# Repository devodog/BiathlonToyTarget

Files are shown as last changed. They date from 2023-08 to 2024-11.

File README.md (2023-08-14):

# Introduction

Watching the biathlon world cup events on tv and sensing the thrill and
excitement of the athletes skiing and especially the shooting
performance, an idea of making a similar toy shooting range target
arrangement for nerf gun, was born.

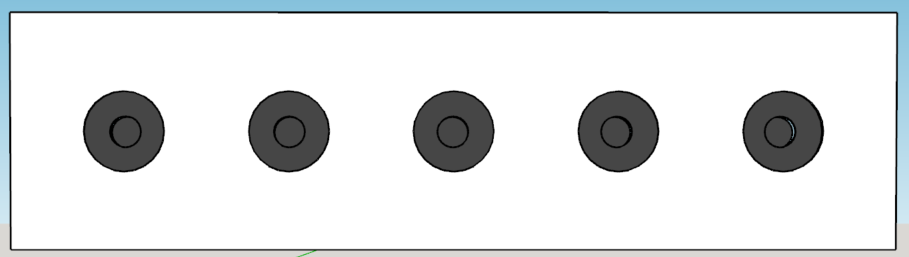
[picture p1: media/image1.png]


So, how to make this toy biathlon shooting range targets that can detect
a nerf gun dart bullet hit?

What technology could be used to register where a nerf gun dart bullet
have hit and what level of precision is needed?

The next thing the toy shooting range target arrangement will need a way
to tell the shooter if she or he has hit the target or not – for the
real biathlon shooting range target, this is done by mechanically
masking / covering the target hit with a white surface, hiding the
targets black surface.

In general, Piezoelectric elements are used to generate / produce sound
waves when a dc voltage is applied to the Piezo element’s terminals –
usually, a high, hearable, frequency sound.

Piezoelectric elements will also accumulate / generate electric charge
flow when exposed to mechanical stress of a certain amount. It is this
effect that can be used to register a nerf gun dart hit on a plane
target surface if the piezo element is mounted on this same target
surface.

Several simple experiments have shown that the signals from the
piezoelectric elements are sufficient for detecting the impulse a nerf
gun dart hit.

The following will describe the electronic and mechanical design for a
Biathlon Toy Target row, emulating the behaviour of the automatic target
hit indicator. Target hit indicator and reset function will be remote
monitored and controlled.

# Target hit indicator

A Nerf-gun dart bullet weighs about 1 g and have a max speed of ~20 m/s.
Guessing that the maximum speed will be some few milli seconds after
“firing” the Nerf-gun and thereafter the Nerf-gun dart bullet speed will
decline rapidly – a function that describe this would be nice.

The speed of the Nerf-gun dart bullet immediately before it hits the
target will determine the power of impact it will cause on the target
plate.

Without doing any advanced analysis of the physics involved, it is easy
to make a similar knock impact on a plane surface as if the same surface
was hit by a nerf gun dart bullet. For example, using a foot long ruler
or a medium size screwdriver, and hitting the plane surface with the end
of the ruler used as a drumstick.

Now, how should the hit sensor piezoelectric element be used? We need to
know more about the electrical characteristics of the piezoelectric
element and to learn about this, we’ll inspect its electrical behaviour
by use of an oscilloscope, when tapping it lightly, for example with end
of a pencil.

## Electrical properties of the piezoelectric element

The piezoelectric element used for this simple test / experiment, was a
1x1x1 cm in size and has two polarized SMD (surface mounted device)
terminals.

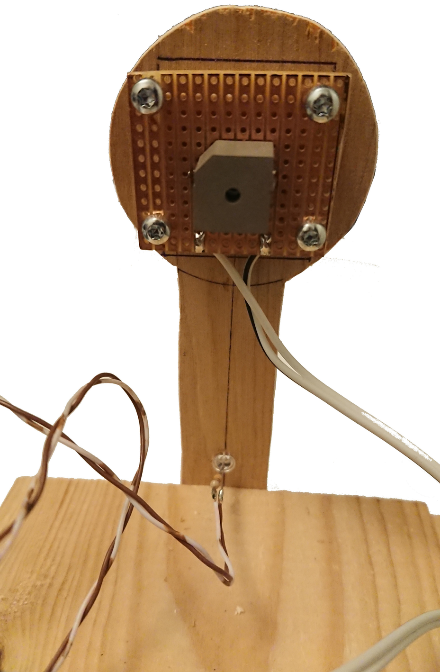
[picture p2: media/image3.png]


Figure : The piezoelectric element soldered to 3x3 cm Vero-board.

As seen in Figure 1, the terminals are connected to two wires, making it
easy to connect to the oscilloscope-probe. The Vero-board is mounted on
a small plywood contour as a 4.5 cm target to imitate a target for nerf
gun dart bullets. The target contour is screwed onto the edge of a board
for mechanical support.

When connected to the oscilloscope probe and taping the target contour
lightly with the one foot ruler, the following pulse train appeared on
the oscilloscope.

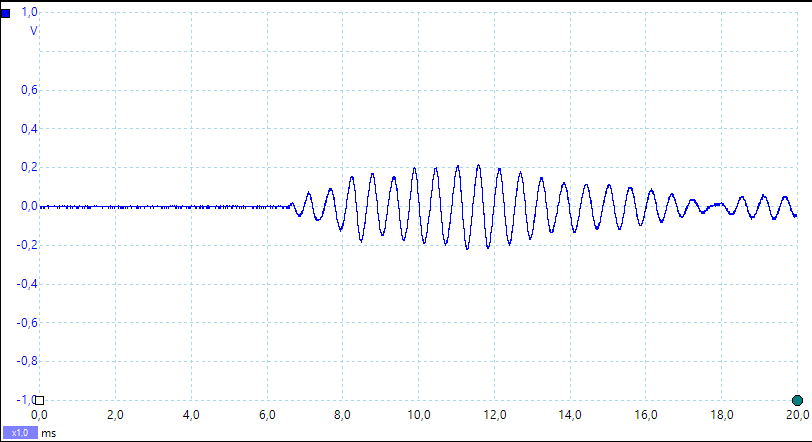
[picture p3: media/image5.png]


Figure 2: Piezo element mount and the pulse train developed by a medium
knock on the mount board.

The signal generated by the piezoelectric element show that it has an
alternating behaviour and for this impact it variates between –200mV and
+200mV. If the physical impact is greater, larger swing can be expected.
Harder impacts can generate up to 4 V peak-to-peak signal. The maximum
swing is not explored.

If the raw output from this piezoelectric element were to be used to
trigger an event, like an interrupt in a microcontroller, this output
signal will certainly challenge any microcontroller General Purpose IO
interface and even cause permanent damage to the interface.  
One trick to avoid this, would be to interconnect a 3v Zener-diode
between the piezoelectric element and the microcontroller GPIO
interface, but then the impact must be quite substantial to excide the
logical threshold for the GPIO interface, and must always be at the same
level of impact. This simple solution is unsuited for a system that
needs to detect a wide range of target hit impacts to allow for various
types of nerf-guns and variable shooting range.

So, to make use of piezoelectric element as target hit sensor, the
output must be refined and amplified, to comply with the requirement of
trigger a wide range of target hit impacts.

## Sensor circuit

Since the piezoelectric element produces an alternating signal, the
signal needs to be rectified and smoothened so that it represents a
single positive pulse. This signal manipulation is usually called “peak
detection”, which is a method to find the highest pulse value among a
series of variable sized pulses.

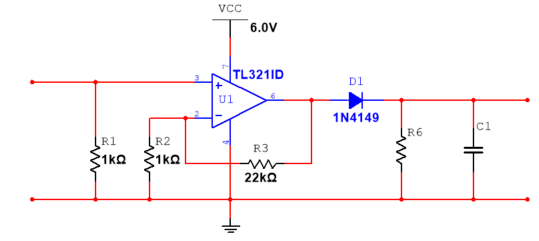
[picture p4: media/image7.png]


Figure : Simple peak detector using an Operational Amplifier.

As this piezoelectric signal will need to be amplifies, it is sensible
to use an Operational Amplifier together with the circuit elements (D1,
C2 & R6) that make the peak detector.

Since the microcontrollers GPIO interface in general accepts only
positive voltages and uses 0V as ground reference, it is most practical
to use a single supply Operational Amplifiers and use supply voltage for
the OpAmps suitable for the MCUs GPIOs.

To detect target hit with variable impact, the rectified and smoothened
signal from the piezoelectric element is forwarded to a level
comparator. The comparator will output Vcc if the input signal from the
peak detector is higher than a reference level, and output 0V if the
input signal is lower than this reference level.

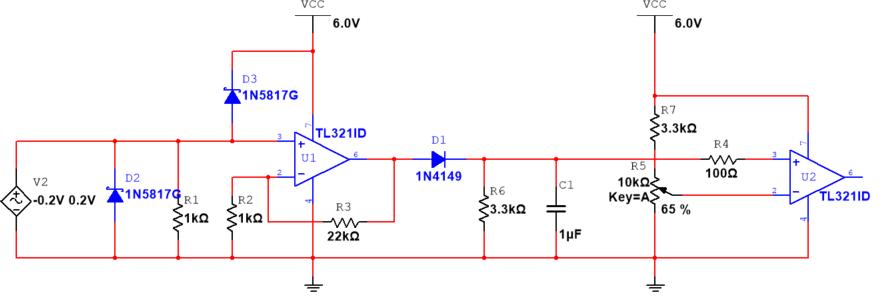
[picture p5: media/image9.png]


Figure : Super simple peak detector followed by a mid-level comparator
to produce a 5V hit trigger/interrupt signal (max outupt is VCC – 1V =
5V according to the data sheet for TL321).

The target hit detector is simple and can be implemented on a small,
printed circuit board, which is easily mounted on the backside of a
piece of 4 to 6 mm plywood, where the frontside of the plywood piece, is
the target to hit.

The impact on the target plate will propagate to the piezoelectric
element soldered onto the PCB, which will produce a single pulse that
can trigger an event on an MCU.

# Detector Hardware solution

The Nerf gun bullet dart hit detector circuit design is manufactured as
a 30x30mm PCB by use of the free CAD tool KiCad. The PCB design
documents are part of the BiathlonToyTargets git repository.

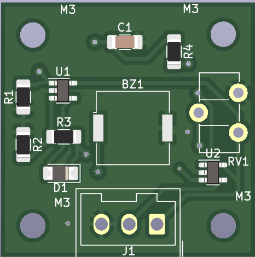
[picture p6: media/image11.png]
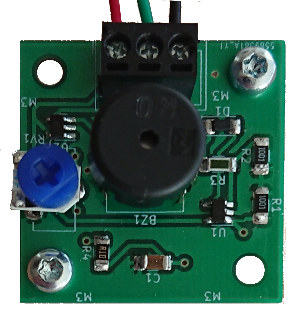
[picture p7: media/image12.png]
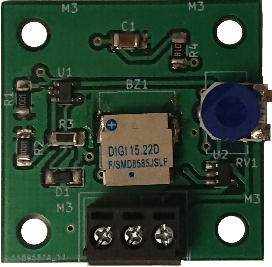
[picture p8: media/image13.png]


Figure : PCB for the target hit detector. The rightmost uses a surface
mounted piezo element.

# Target hit indication

The shooting range biathlon targets indicate immediately if one is hit,
by covering the black surface that represents the target. To imitate
this functionality, a small servo motor will rotate a circle shaped 3 mm
MDF plate, called the Cover-plate, between the target surface and the
front plate.

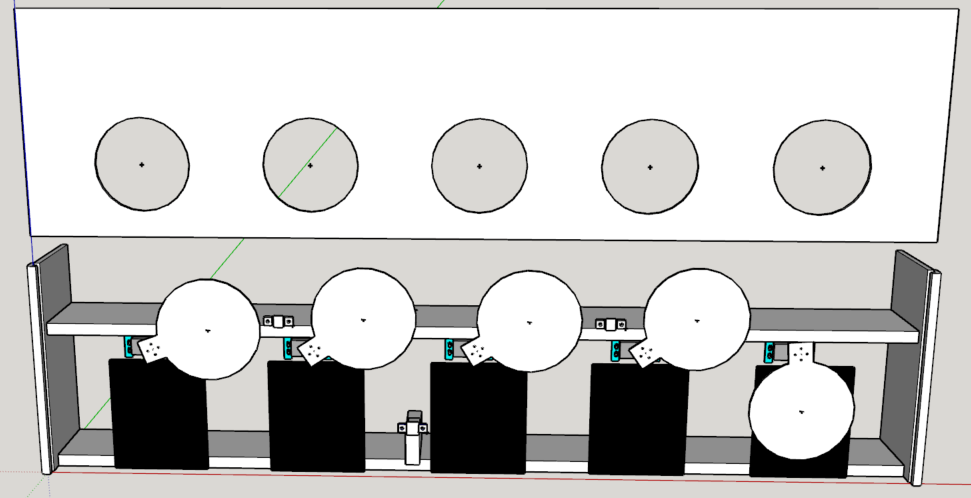
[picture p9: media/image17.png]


Figure : The construction of the biathlon toy target stand.

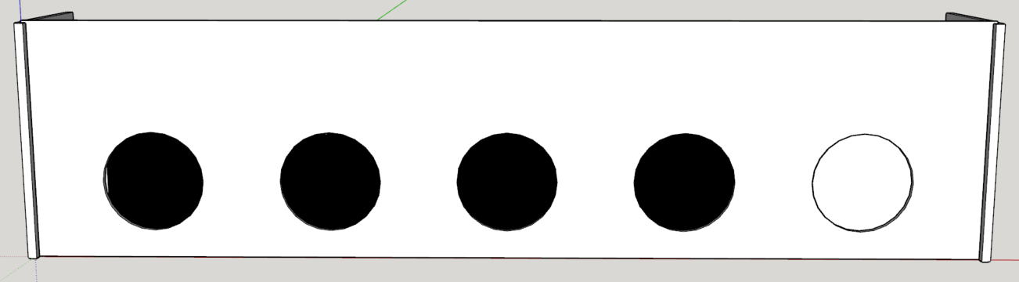
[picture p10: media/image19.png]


Figure : The biathlon toy targets with one hit indication - the
rightmost target surface is covered by its cover plate.

## Shooting range biathlon toy targets construction

The biathlon toy targets stand with cover plates for hit indication, is
a simple construction made from 16 mm floorboards of fir tree and a 6 mm
plywood target stand cover with 5 circular formed “windows” exposing the
biathlon toy target surfaces.

From Figure 5, two floorboards form as top end bottom of the
construction, providing support for both the target surface for the nerf
gun dart bullets (the lower floorboard), and for mounting the servo
motors for each hit indicator cover plate. The cover plate is attached
to the servo motors spine shaft by a spine socket fixture to rotate it
to cover the target “window”.

## Servo motor requirements

The servo motor must be able to rotate the target cover, meaning that it
has to provide sufficient torque for this operation. The size and weight
of the target cover determines the necessary torque needed.  
As the biathlon standing target diameter is 11.5 cm, the target cover
must have a slightly larger diameter and a diameter of 13 cm will
probably be a practical size. Alternative materials can be used, but for
the current prototype, 3 mm MDF board will be used. This material’s
density is approximately 820 kg/m<sup>3</sup>, which gives that MDF
target cover described above will weigh approximately …..

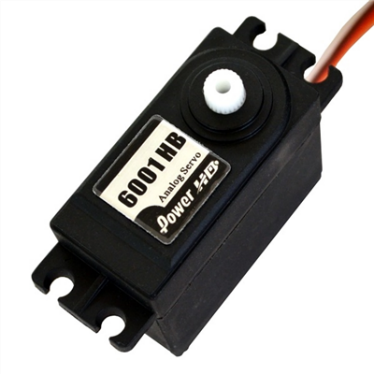
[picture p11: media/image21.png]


Figure 8: Servo motor (<https://www.elefun.no/p/prod.aspx?v=15938>) to
move the target cover. The 6 mm plywood target cover can and will be
replaced with 3 mm MDF material.

The volume of the target cover = d·πr<sup>2</sup> = 0.003 m · π · (0.065
m)<sup>2</sup> = <u>12.68 · 10<sup>-6</sup> m<sup>3</sup></u>

- The total weight of the target cover is approximately **33 grams**.

- Centre of mass relative to servo shaft (13 cm/2 + 1 ∽ **7.5 cm**)

- Required servo torque = 33g \* 7.5 ~ **0,25 kg/cm**

So, using an analogue that outputs a torque of 6.7 kg / cm would
certainly be more than sufficient, which the Power HD-6001HB will do.

## Servo motor control and operation

In general, servo motors are controlled by a 50 Hz PWM signal, usually
provided by a microcontroller. The servo motor’s interface contains of
6V and Ground connection in addition to the PWM signal wire.

# Solution infrastructure

The biathlon toy target solution infrastructure is shown in …

Figure 9: Biathlon toy target hardware infrastructure for automatic hit
detection and indication.

# Wiring plan

Every target will need power and two signal leads. The power will be
distributed from a 6V battery pack onto a power bus that is connected
(some daisy chained) five individual connection panels.

Each of these connection panels will then provide power to both target
sensor elements and the servo motor. The signal leads from the sensor
and to the servo will also be connected this connection panel and wired
to the proper GPIO on the MCU.

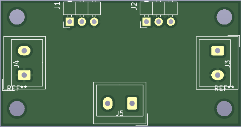
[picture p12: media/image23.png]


Figure : Power and signal distribution.

Important to supply each power connection with an appropriated sized
capacitor for stable power source for the hit sensor circuits.

# Microcontroller considerations

The construction of the prototype Biathlon Toy Targets with automatic
hit detection and indication, will so far need a microcontroller that
has at least 10 General Purposed IO ports for handling the shooting
situation. The Biathlon Toy target system must also have a way of
resetting the target covers, preferable from a distance, in addition to
reading the hit results digitally and forward these to another device or
computer. A possible option for this last requirement could be to use a
simple UART, which is often included in microcontrollers.

## Interrupt driven operation for hit detection

Since there are 5 targets that can be hit in any order, the hit sensor
should trigger on an interrupt that reads the signal status on all
targets simultaneously to determine which has been hit. This
functionality will require that 5 of GPIOs, in the selected MCU, used
for hit-detection, must have the ability to trigger an interrupt based
on a signal level change.

## PWM driver for hit indication

The servo motor will tbd

## Wireless and/or wired communication for reset, collecting results and test functions

The easiest way of implementing a communication channel between the MCU
and a PC is to use the legacy serial port operation, since this is based
on the UART functionality, which is also often found integrated in many
microcontrollers.

Implementing the bi-directional operation of this functionality,
commands can be given from a remote terminal, like reset target covers,
and feedback can be received for both hit results and debugging needs.

# Microcontroller used for the Biathlon Toy Target prototype

The MCU used for the Biathlon Toy Target is a 8-bit mcu Attiny 1634 from
Microchip. This is tiny device with 18 programmable IO pins, 16k flash
memory and 1k random access memory, which is more than sufficient to
implement the necessary software operations for the prototype Biathlon
Toy Targets with automatic hit detection and indication.

## Integrated Development Environment – Atmel Studio 7.0

Programmer and debugger… Atmel Ice

# Remaining work on the prototype.

1)  Arranging all loose wires onto the target structure by use of cable
    clips or glue.

2)  Make passage for the wires in wood structure.

3)  Glue spacer (3 mm MDF) onto the centre of the target cover servo
    mount point…

4)  Clue spacer (4 or 3 mm MDF) onto the centre of the back of the
    target cover for mechanical support it shot at when it covers an
    already hit target.

5)  Make an open panel for mounting power jack for charging the battery
    pack, a toggle switch for power on/off the unit.

6)  Make a Veroboard for connecting the power jack and power switch the
    MCU and battery pack.

7)  Solder a 10µF capacitor to all sensor and servo power distribution
    boards.

8)  Test functionality with a new improved front board centre “clamping”
    (this is to make the front board as straight as possible)

9)  <u>IMPROVEMENT</u>: Use the analogue input to measure the battery
    voltage and show it through a terminal command.

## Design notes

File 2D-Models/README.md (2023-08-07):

This folder contains 2D CAD (dxf-files) description of the cover plates for automatic Biathlon Toy Target hit indication.

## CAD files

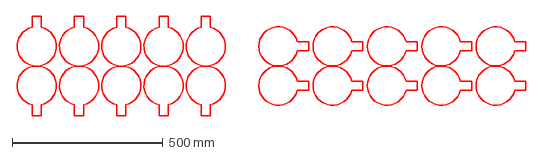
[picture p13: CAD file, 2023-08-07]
2D-Models/TargetCover13cm.dxf
1688.4 x 330.0 mm

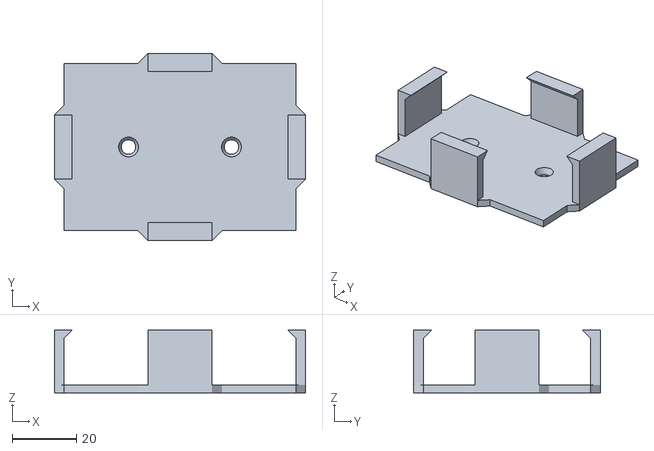
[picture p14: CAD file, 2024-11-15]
3D-Models/6vNiMH-Mount.stl
78.0 x 58.0 x 19.5

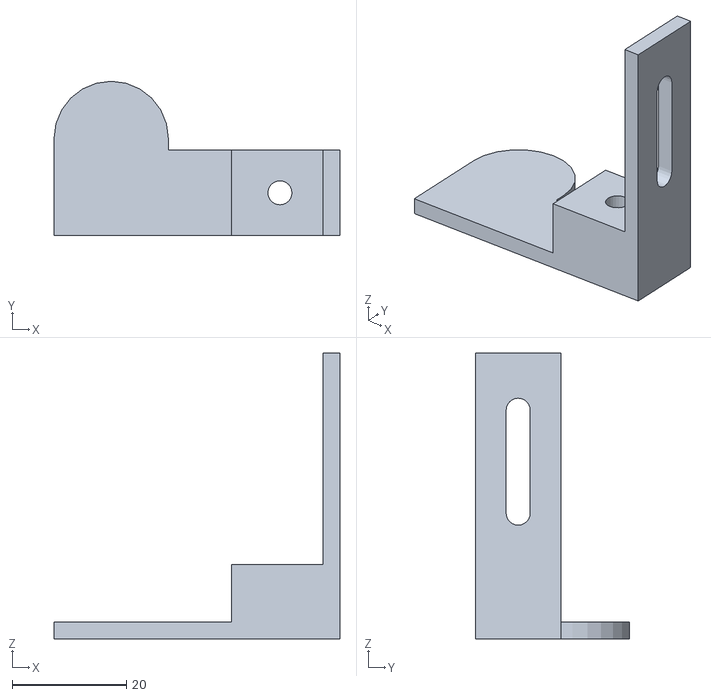
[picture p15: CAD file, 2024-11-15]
3D-Models/servoSproketSupportV2.stl
50.0 x 27.0 x 50.0

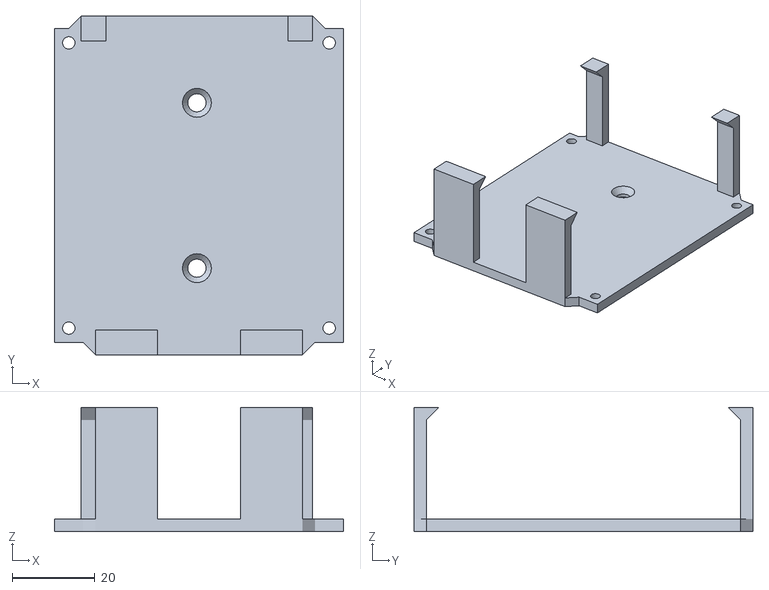
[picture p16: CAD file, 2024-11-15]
3D-Models/casing_mount.stl
70.0 x 82.0 x 30.0

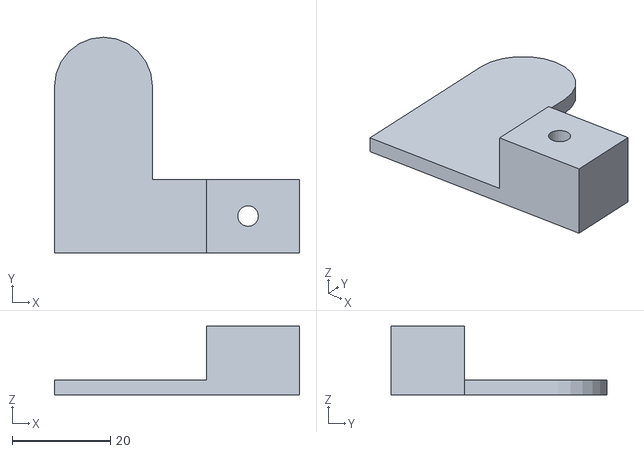
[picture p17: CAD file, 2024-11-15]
3D-Models/servoSproketSupportCenterV2.stl
50.0 x 44.0 x 14.0

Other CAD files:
3D-Models/6vNiMH-Mount.skp
3D-Models/ServoMountVer02.skp
3D-Models/servoSproketSupportCenterV2.skp
3D-Models/servoSproketSupportV2.skp

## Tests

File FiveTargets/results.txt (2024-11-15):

Start nr1: 00:03:01.96 s
Start nr2: 00:00:29.33 s
Start nr3: 00:00:20.05 s
Start nr4: 00:00:26.79 s
Start nr5: 00:00:28.93 s
Start nr6: 00:00:27.23 s
Start nr7: 00:01:19.60 s
Start nr8: 00:00:26.33 s
Start nr9: 00:00:44.39 s
Start nr10: 00:00:14.78 s
Start nr11: 00:00:57.99 s
Ole Brumm: 03:01.96
Ole Brumm: 03:01.96
Ole Brumm: 03:01.96
Snurre Sprett: 00:29.33
Petter Smart: 00:20.05
Petter Nortug: 00:26.79

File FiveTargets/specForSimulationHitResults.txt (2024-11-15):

Can you suggest a python script that provides a user command prompt that is to handle two 
commands, "send" or "exit". The exit command is to terminate the script, but the
send command should read one line from a text file, named testdata.txt, and send this to 
com port in windows. For each send command the script shall read the next line and send this
also to the com port, until it reads end of file, which will terminate the script.

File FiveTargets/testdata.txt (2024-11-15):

Time used: 00:01:01.96 s
Time used: 00:00:23.33 s
Time used: 00:00:21.05 s
Time used: 00:00:22.79 s
Time used: 00:00:24.93 s
Time used: 00:00:25.23 s
Time used: 00:01:12.60 s
Time used: 00:00:21.33 s
Time used: 00:00:24.39 s
Time used: 00:00:24.78 s
Time used: 00:00:57.92 s

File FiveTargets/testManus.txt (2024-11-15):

Connect 2 usb-to-rs232 to 2 usb-ports on a pc
Interconnect the 2 rs232 interfaces with a crossover cable.

Launce the cmd (command line prompt in Windows) and enter the directory 
fiveTargets. This directory that should contain the following files:
sim.py
start.py
testdata.txt
and this file testManus.txt

Launche a seconf cmd and and enter the same directory, fiveTargets.
In cmd #1 enter the following command: C:\Users\user\fiveTarget>py sim.py
In cmd #2 enter the following command: C:\Users\user\fiveTarget>py start.py

open browser with http://localhost/midtskips.no/uiaod/index.html
or
open browser with http://midtskips.no/uiaod/index.html

Test execution:
In cmd #2 enter a name
in cmd #1 enter the command: send

Check:
Verify that the web page at ...midtskips.no/uiaod/index.html has been updated 
with the name entered with a new time

repeat the test execution 10 times

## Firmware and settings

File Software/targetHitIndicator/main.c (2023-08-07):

/*
 * main.c
 *
 * Created: 13.01.2022 14:22:30
 * Author : Dag
 *
 * Source code for the tinyWatcher board based on the ATtiny1634 MCU from Atmel
 * (now Microchip).
 *
 * ****************************************************************************
 * CODE TO HANDEL PIN CHANGE INTERRUPT WHICH WILL PRODUCE PWM TO A SERVO MOTOR 
 * TO ROTATE THE SERVO MOTOR'S SHAFT MORE THAN 100 DEG. 
 * ****************************************************************************
 *
 * GPIO Port B
 * PB2
 * PB3(output): D100 (BLUE LED)
 *
 * GPIO Port C
 * PC0(output): 
 * PC2(output): LED2
 *
 *
 */ 
#ifndef F_CPU
// define cpu clock speed if not defined
#define F_CPU 12000000UL
#endif

#include <avr/io.h>

#include <string.h>
#include <avr/interrupt.h>
#include <avr/sleep.h>
#include <util/delay.h>
#include <stdbool.h>

#include "appver.h"
#include "serial.h"

#define UNIT_STATUS_LED_ON() PORTB |= (1<<PORTB3)
#define UNIT_STATUS_LED_OFF() PORTB &= ~(1<<PORTB3)

#define UNIT_STATUS_LED1_ON() PORTC |= (1<<PORTC0)
#define UNIT_STATUS_LED1_OFF() PORTC &= ~(1<<PORTC0)

#define UNIT_STATUS_LED2_ON() PORTC |= (1<<PORTC2)
#define UNIT_STATUS_LED2_OFF() PORTC &= ~(1<<PORTC2)

char termInputBuffer[80];
bool cmdComplete;

bool hit;
uint8_t cmdLength = 0;
volatile uint8_t targetId0 = 0; // 

uint8_t targetState[6];

void ledBlink()
{
   UNIT_STATUS_LED_ON();
   _delay_ms(150);
   UNIT_STATUS_LED_OFF();
   _delay_ms(150);
}

void led1Blink()
{
   UNIT_STATUS_LED1_ON();
   _delay_ms(150);
   UNIT_STATUS_LED1_OFF();
   _delay_ms(150);
}

void led2Blink()
{
   UNIT_STATUS_LED2_ON();
   _delay_ms(150);
   UNIT_STATUS_LED2_OFF();
   _delay_ms(150);
}

char *cmdList[] = {"servo", "info"};
// servo   : 1 arg 'h' Hit indication or 'r' reset operation

enum commands {
   SERVO,
   INFO
} COMMANDS;


void promt() {
   printf("\nbtt> ");
}


   
// _delay_us(2200); max counterclockwise (165 degrees)
// _delay_us(1300); middle? (90 degrees)
void moveServo(char targetEvent, uint8_t targetCover) {
   printf("\nstate=%x,,,target=%d\n", (uint8_t)targetState, targetCover);
   
   for (int i=0; i<20; i++) {
      switch(targetCover) {
         case 1:
            PORTA |= 1<<PORTA5;
            break;
         case 2:
            PORTA |= 1<<PORTA6;
            break;
         case 3:
            PORTB |= 1<<PORTB2;
            break;
         case 4:
            PORTB |= 1<<PORTB1;
            break;
         case 5:
            PORTC |= 1<<PORTC0;
            break;
         default:
            return;
      }
      
      if (targetEvent == 'r') {
         _delay_us(2000);
      }
      else {
         _delay_us(1000);
      }
      
      switch(targetCover) {
         case 1:
			 PORTA &= ~(1<<PORTA5);
			 break;
         case 2:
			 PORTA &= ~(1<<PORTA6);
			 break;
         case 3:
			 PORTB &= ~(1<<PORTB2);
			 break;
         case 4:
			 PORTB &= ~(1<<PORTB1);
			 break;
         case 5:
			 PORTC &= ~(1<<PORTC0);
			 break;
         default:
         return;
      }
       _delay_ms(20); 
   }
   if (targetEvent == 'r') {
      targetState[targetCover] = 0;
   }
   else {
      targetState[targetCover] = 1;
   }
 }

uint8_t executeCmd(char *termInput, int cmdLength) {
   int i = 0;
   for (; i < sizeof(cmdList); i++) {
      if (strncmp(cmdList[i], termInput, strlen(cmdList[i])) == 0) {
         break;
      }
   }
   
   if (i >= sizeof(cmdList)) {
      printf("\n%s is not recognized", termInput);
      promt();
   }
   else {
      switch (i) {
         case SERVO:
		   // If reset all...
            if ((termInput[6] == 'r')&&(termInput[8] == 'a')) {
			      for (int i = 1; i < 6; i++) {
				      if(targetState[i]==1) {
					      moveServo('r', i);
					      targetState[i] = 0;
					      printf("\nMoving servo...");
				      }
			      }
		      }
		      // If set all as hit...
		      else if ((termInput[6] == 'h')&&(termInput[8] == 'a')) {
			      for (int i = 1; i < 6; i++) {
				      if(targetState[i]==0) {
					      moveServo('h', i);
					      targetState[i] = 1;
					      printf("\nMoving servo...");
				      }
			      }
		      }
		      // set or reset specific...
		      else {
			      moveServo(termInput[6], termInput[8]-48);
		      }
            promt();
         break;
         
         case INFO:
            printf("\nBiathlonToyTarget ver. %d.%d build: %d\n", MAJOR_VERSION, MINOR_VERSION, BUILD);
            for (int i=1; i<6; i++) {
               printf("Target[%d] state: %d\n", i, targetState[i]);
            }
            // Info about the current target status?
            promt();
         break;
         
         default:
            printf("\nNOP[i=%d]", i);
            promt();
         break;
      }
   }
   return 0;
}

void init() {
   // Initialize PORT PA5 & PA6 as output (PWM to servos).
   DDRA |= (1<<PORTA5)|(1<<PORTA6);
   
   //DDRA &= ~(1<<PORTA0); // Pin Change Input interrupt
     
   DDRC |= (1<<PORTC0)|(1<<PORTC2); // PC0 for PWM to servo. C2 for LED.
   
   DDRB |= (1<<PORTB1)|(1<<PORTB2)|(1<<PORTB3);  // PB1 & PB2 for PWM to servos. PB3 for LED.
   
   hit = false; // Target status
   
   
   // Assign that address for my stdout function...
   stdout = &mystdout;
   USART_Init();
   
   // Reset all target covers.
   moveServo('r', 'a');
   
   // Initialize the pin-change interrupts...
   // We'll start with one pin which is PA6 = PCI6
   
   // MCUCR – MCU Control Register
   MCUCR |= 0x1; // Any logical change on INT0 generates an interrupt request
   // GIMSK – General Interrupt Mask Register
   GIMSK |= 0x8; // Pin Change Interrupt Enable 0 - for all pins of port A.
   PCMSK0 |= 0x1f; // Pin Change Enable Mask on PORTA => 0b0001 1111 = (PA0 & PA1 & PA2 & PA3 & PA4)
   
   sei();
   
   // Boot printout...
   printf("Version.%d.%d-b:%d\n", MAJOR_VERSION, MINOR_VERSION, BUILD);
   for(int8_t i=5; i>0; i--)
   {
      if (i==1) {
        printf("\n");
      }
      else {
        printf(".");
      }
      ledBlink();
   }
   promt();
}

int main(void)
{
   init();
   uint8_t target = 0;
   // Received a command from the serial com terminal 
   while (1) {
      if(cmdComplete) {
         cmdComplete = false;
         if (cmdLength == 0) {
            promt();
            continue;
         }
         executeCmd(&termInputBuffer[0], cmdLength);
         memset(termInputBuffer, 0, 80);
      }
      
      if (hit) {
         // Pin Change interrupt for PORT A only, using pin PA0 to PA4 as hit indicators. 
         printf("\nHIT on target %x", targetId0);
         for (int i = 0; i < 5; i++) {
            if ((targetId0 >> i) == 1)
               target = i+1;
         }
		 
		 if ((target < 6) && (target > 0)) {
			moveServo('h', target);
		 }
       promt();
		 hit = false;
      }
    }
}

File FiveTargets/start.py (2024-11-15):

from urllib import response
import serial # type: ignore
import time
import json
import requests # type: ignore

# The API endpoint
url = "http://midtskips.no/uiaod/receiver.php"

def read_from_com_port(com_port, baud_rate, output_file, current_name):
        
    # Open the serial port
    with serial.Serial(com_port, baud_rate, timeout=1) as ser:    
        
        print(f"Listening on {com_port} at {baud_rate} baud...")
        
        while True:
            # Read a line from the COM port
            line = ser.readline().decode('ascii').strip()
            
            if line:
                print(f"Received: {line}")
                # Check if the line contains the time result
                if "Time used: " in line:
                    # Extract the time result, but ignoring the hour element
                    time_result = line.split(": 00:")[1]
                    time_result = time_result.strip(" s")
                    # Data to be sent
                    data = {}
                    data['Name'] = current_name
                    data['Time'] = time_result
                    json_data = json.dumps(data)
                    print(json_data)
                    
                    # A POST request to the API
                    response = requests.post(url, json=data)

                    # Print the response
                    print(response.text)

                    # Write the name and time result to the file
                    with open(output_file, 'a') as file:
                        file.write(f"{current_name}, {time_result}\n")
                        file.flush()  # Ensure data is written to the file immediately
                    print(f"Logged: {current_name}, {time_result}")
                    return
            # Optional: Add a small delay to avoid overwhelming the CPU
            time.sleep(0.1)

if __name__ == "__main__":
    # Configure your COM port and baud rate
    COM_PORT = 'COM14'  # Change this to your COM port
    BAUD_RATE = 9600    # Change this to your baud rate
    #OUTPUT_FILE = 'results.txt'  # Change this to your desired output file
    OUTPUT_FILE = "C:/xampp/htdocs/midtskips.no/uiaod/results.txt"
    #print("Enter names to link with time results. Type 'exit no' to stop.")
    portNumber = input("Enter com-port to use [1,2,3,..,n]: ").strip().lower()
    if (portNumber.isdigit()):
        COM_PORT = 'COM'+portNumber
    else:
        print("COM",portNumber," is not valid port number! Exiting.")
        exit()
    
    print("Will use", COM_PORT)

    while True:
        # Prompt the user for a name
        current_name = input("Enter a name (or 'exit' to finish): ")
        
        if current_name.lower() == "exit":
            print("Exiting the program.")
            break
        else:
            # Start reading from the COM port for the current name
            try:
                read_from_com_port(COM_PORT, BAUD_RATE, OUTPUT_FILE, current_name)
            except KeyboardInterrupt:
                print("Program terminated by user.")
            except Exception as e:
                print(f"An error occurred: {e}")

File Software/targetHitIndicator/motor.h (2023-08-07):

/*
 * motor.h
 *
 * Created: 24.04.2021 14:03:24
 *  Author: Dag
 */ 

#ifndef MOTOR_H_
#define MOTOR_H_

#define MICRO_STEP 200
#define SEQUENCE_STEP 50

#define IDLE_INDICATION 60
#define SPEED_DIVIDER 20
#define MAX_SPEED 80

//#define DYNAMIC_SPEED_CONTROL 1
#ifndef DYNAMIC_SPEED_CONTROL
#define MINIMUM_SIGNAL_DURATION 2350   // microseconds - without dynamic speed
// adjustment...
#else
#define MINIMUM_SIGNAL_DURATION 100
// Sampling the adc takes more than one millisecond so the dynamic speed
// adjustment will not give max speed to the motor.
#endif

#define MAX_SIGNAL_DURATION ((1024/SPEED_DIVIDER)+1)
#define UNIT_STATUS_LED_ON() PORTB |= (1<<PORTB3)
#define UNIT_STATUS_LED_OFF() PORTB &= ~(1<<PORTB3)

#define UNIT_STATUS_LED1_ON() PORTC |= (1<<PORTC0)
#define UNIT_STATUS_LED1_OFF() PORTC &= ~(1<<PORTC0)

#define UNIT_STATUS_LED2_ON() PORTC |= (1<<PORTC2)
#define UNIT_STATUS_LED2_OFF() PORTC &= ~(1<<PORTC2)

// Step motor operation configuration
typedef struct {
   bool man;            // Manual operation...
   uint8_t dir;         // the direction of the rotation
   uint16_t speed;		//
   uint16_t turn;       // number of rotations to execute
   uint16_t dur;        // duration of continue motor operation
   uint16_t delay;      // delay before executing the motor operation
   uint16_t refpos;     // reference position
   uint16_t steps;      // current or next position relative to the reference position (get/set)
   uint16_t degree;     // current or next position in degrees relative to the reference position
   uint8_t error;       // last error number
} STEP_MOTOR_CONFIG;

void promt();
void initStepMotorConfig(STEP_MOTOR_CONFIG* cfg);
uint8_t setMotorParams(char *arg, char *value);
uint8_t executeCmd(char *termInput, int cmdLength);
void noOperation();
int setStepMotorSpeed();
bool isStepMotorHalted();
void run(int dir, int speed, int numOfSteps);
void moveServo(char targetState);

#endif /* MOTOR_H_ */

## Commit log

2023-08-07 Including initial some 2D and 3D models
    [ServoMountVer0.skp, TargetCover13cm.dxf, servoMountVer0.stl]
2023-08-07 Hardware and software included in this repository
    [TargetHitDetector.kicad_pcb, TargetHitDetector.kicad_sch]
2024-11-15 Hi-detector hardware design is currently moved.
    [TargetHitDetector.kicad_pcb, TargetHitDetector.kicad_sch]
2024-11-15 Added 3D models and python script directory (for game run).
    [6vNiMH-Mount.skp, 6vNiMH-Mount.stl, ServoMountVer0.skp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]
